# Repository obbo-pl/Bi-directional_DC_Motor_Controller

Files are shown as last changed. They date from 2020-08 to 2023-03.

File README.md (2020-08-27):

# Bi-directional_DC_Motor_Controller
RC Bi-directional DC Motor Speed Controller

##### Main features:

- supply voltage: 7.0 - 20.0V,
- average current: 10A, maximum instantaneous current: 140A,
- BEC 5V 1,2A,
- protection against reverse battery polarity,
- on/off switch controlled by logic level,
- calibration of the adjustment range with automatic saving of settings,
- protection against engine starting when starting the system,
- Cut-off, engine shutdown or speed reduction,
- choice of: linear and nonlinear RPM control characteristics,
- speed regulation smoothing filter,
- Fail-safe, engine shutdown in the event of signal loss,
- 3 quick configuration jumpers,
- brake,
- parameter configuration via serial port (9600bps).

### Hardware & Firmware.

These sections provide information on building a hardware, including schematics, PCBs, and firmware.

For more information: [www.obbo.pl](http://obbo.pl/dc-controller)

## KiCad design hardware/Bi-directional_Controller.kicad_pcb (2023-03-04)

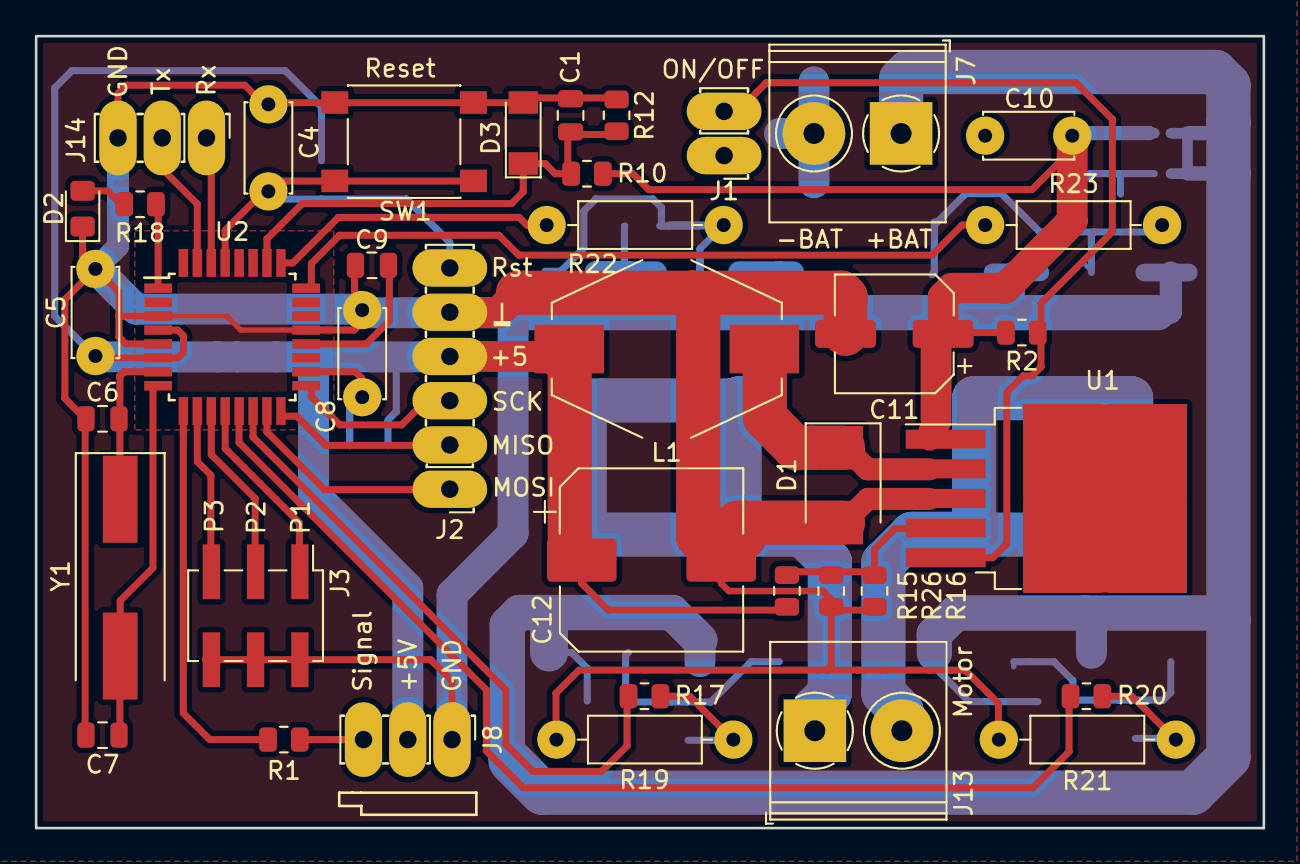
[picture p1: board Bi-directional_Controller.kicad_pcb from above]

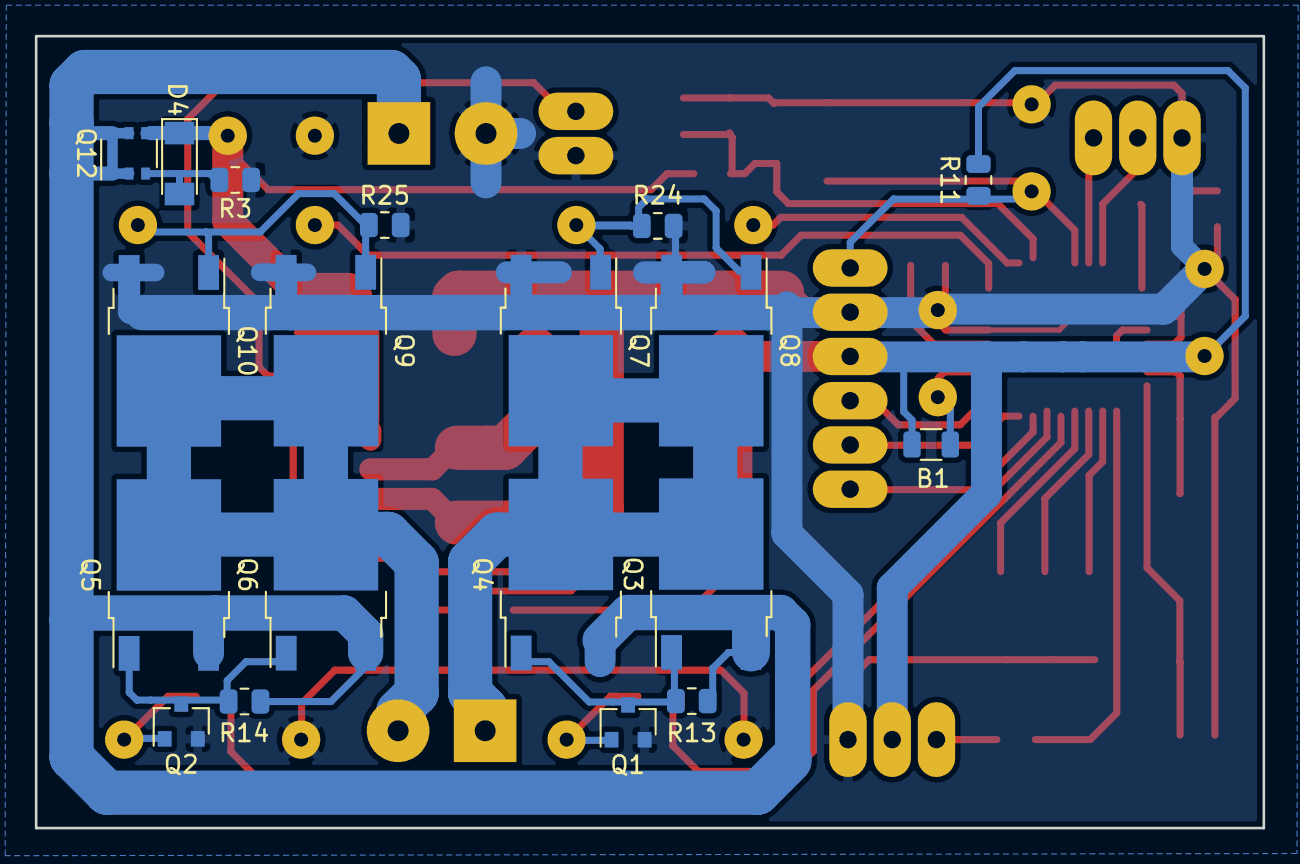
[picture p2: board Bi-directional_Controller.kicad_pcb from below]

Board: 2 copper layers, 70.5 x 45.5 mm, 58 parts (19 on the bottom side), 38 nets.

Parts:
B1: bead; L_0805K
C1, C9: 100n; C_0805_2012Metric
C4, C5, C8, C10: 100n; C_Disc_D5.0mm_W2.5mm_P5.00mm_PAD
C6, C7: 15p; C_0805_2012Metric
C11: 100u/35V; CP_Elec_6.3x5.9
C12: 1000u/10V; CP_Elec_10x10
D1: B340; D_SMB
D2: LED; LED_0805_2012Metric_Pad1.15x1.40mm_HandSolder
D3: 4V7; D_MiniMELF
D4: 8v2; D_MiniMELF
J1: ON/OFF; PinHeader_1x02_P2.54mm_Vertical_PAD
J2: Conn_01x06; PinHeader_1x06_P2.54mm_Vertical_PAD
J3: Conn_02x03_Odd_Even; PinHeader_2x03_P2.54mm_Vertical_SMD
J7: BAT 12V; TerminalBlock_Degson_DG128-5.0-02P
J8: CH1; PinHeader_1x03_P2.54mm_Vertical_PAD
J13: MOTOR; TerminalBlock_Degson_DG128-5.0-02P
J14: Serial; PinHeader_1x03_P2.54mm_Vertical_PAD
L1: 100uH; L_SMD_Ferrite_X13mm_Y10mm_H5mm_HandSoldering
Q1, Q2: BSS138; SOT-23
Q3, Q4, Q5, Q6: AOD403; TO-252-2-DPAK
Q7, Q8, Q9, Q10: AOD240; TO-252-2-DPAK
Q12: AO6401A; TSOP-6_1.65x3.05mm_P0.95mm
R1, R18: 330; R_0805_2012Metric
R2, R3, R11, R15: 10k; R_0805_2012Metric
R10: 22k*; R_0805_2012Metric
R12, R26: 4k7; R_0805_2012Metric
R13, R14, R24, R25: 22k; R_0805_2012Metric
R16: 11k*; R_0805_2012Metric
R17, R20: 220; R_0805_2012Metric
R19, R21: 22k; R_Axial_DIN0207_L6.3mm_D2.5mm_P10.16mm_Horizontal_PAD
R22, R23: 220; R_Axial_DIN0207_L6.3mm_D2.5mm_P10.16mm_Horizontal_PAD
SW1: RESET; SW_SPST_PTS645
U1: LM2576HVS-5; TO-263-5_TabPin6
U2: ATmega8-16AU; TQFP-32_7x7mm_P0.8mm
Y1: 16MHz; Crystal_SMD_HC49-SD_HandSoldering

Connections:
+5V: B1.1, C5.1, C12.1, J2.4, J8.2, L1.2, R11.1, R15.2, U2.4, U2.6
+12V: C10.1, C11.1, D4.1, Q12.4, R2.2, R10.1, U1.1
CH1: R1.1, U2.9
DIR_L: R20.2, U2.13
DIR_R: R17.2, U2.14
GND: C1.2, C4.2, C5.2, C6.2, C7.2, C8.2, C9.2, C10.2, C11.2, C12.2, D1.2, D2.1, D3.2, J1.1, J2.5, J3.2, J3.4, J3.6, J7.2, J8.1, J14.3, Q1.2, Q2.2, Q7.3, Q8.3, Q9.3, Q10.3, R3.1, R12.2, R16.2, R19.1, R21.2, R24.1, R25.1, R26.1, SW1.1, U1.3, U2.3, U2.5, U2.21
unnamed: B1.2, C8.1, U2.18
unnamed: C4.1, J2.6, R11.2, SW1.2, U2.29
unnamed: C6.1, U2.7, Y1.1
unnamed: C7.1, U2.8, Y1.2
unnamed: C9.1, U2.20
unnamed: D1.1, L1.1, U1.2
unnamed: D2.2, R18.2
unnamed: D4.2, Q12.3, R3.2
unnamed: J1.2, R2.1, U1.5
unnamed: J2.1, U2.15
unnamed: J2.2, U2.16
unnamed: J2.3, U2.17
unnamed: J3.1, U2.12
unnamed: J3.3, U2.11
unnamed: J3.5, U2.10
unnamed: J8.3, R1.2
unnamed: J13.1, Q3.2, Q4.2, Q7.2, Q8.2
unnamed: J13.2, Q5.2, Q6.2, Q9.2, Q10.2
unnamed: J14.1, U2.30
unnamed: J14.2, U2.31
unnamed: Q1.1, R17.1, R19.2
unnamed: Q1.3, Q3.1, Q4.1, R13.1
unnamed: Q2.1, R20.1, R21.1
unnamed: Q2.3, Q5.1, Q6.1, R14.1
unnamed: Q7.1, Q8.1, R22.2, R24.2
unnamed: Q9.1, Q10.1, R23.2, R25.2
unnamed: R15.1, R16.1, R26.2, U1.4
unnamed: R18.1, U2.1
PULS_L: R22.1, U2.25
PULS_R: R23.1, U2.24
V_BAT: J7.1, Q3.3, Q4.3, Q5.3, Q6.3, Q12.1, Q12.2, Q12.5, Q12.6, R13.2, R14.2
V_TEST: C1.1, D3.1, R10.2, R12.1, U2.26

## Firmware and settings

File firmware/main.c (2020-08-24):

/*
 * main.c
 *
 * Created: 12.08.2019 13:17:11
 * Atmel Studio 6 (Version: 6.2.1563 - Service Pack 2)
 * AVR/GNU C Compiler : 4.8.1
 *  Author: Krzysztof Markiewicz
 *  www.obbo.pl
 *
 * This program is distributed under the terms of the GNU General Public License
 */ 

#include <avr/io.h>
#include <avr/interrupt.h>
#include <util/delay.h>
#include <avr/eeprom.h>
#include <avr/pgmspace.h>
#include <stdlib.h>
#include <stdbool.h>
#include "main.h"
#include "lowpass_filter.h"
#include "types.h"
#include "delays.h"
#include "cbuffer.h"
#include "usart.h"
#include "terminal.h"
#include "terminal_commands.h"
#include "adconversion.h"
#include "bridge.h"
#include "led.h"


// resource:
// timer0 - common timers
// timer1 - checks the signal from the receiver
// timer2 - motor PWM
// ADC - checks battery voltage
// UART - serial communication (9600) for advanced configuration



#define VERSION_MAJOR				"1"
#define VERSION_MINOR				"0"
#define DEVICE_INFO_SIZE			40
const char DEVICE_INFO[DEVICE_INFO_SIZE]	PROGMEM = "DC " VERSION_MAJOR "." VERSION_MINOR " (build: " __DATE__ " " __TIME__ ")\n\r";

uint8_t EEMEM EEMEM_curve[256] = {0x00, 0x06, 0x0c, 0x12, 0x12, 0x12, 0x12, 0x12, 0x12, 0x12, 0x12, 0x12, 0x12, 0x12, 0x12, 0x13,
				  0x13, 0x13, 0x13, 0x13, 0x13, 0x13, 0x14, 0x14, 0x14, 0x14, 0x15, 0x15, 0x15, 0x15, 0x16, 0x16,
				  0x16, 0x16, 0x17, 0x17, 0x17, 0x18, 0x18, 0x18, 0x19, 0x19, 0x19, 0x1a, 0x1a, 0x1b, 0x1b, 0x1b,
				  0x1c, 0x1c, 0x1d, 0x1d, 0x1e, 0x1e, 0x1e, 0x1f, 0x1f, 0x20, 0x20, 0x21, 0x21, 0x22, 0x23, 0x23,
				  0x24, 0x24, 0x25, 0x25, 0x26, 0x27, 0x27, 0x28, 0x28, 0x29, 0x2a, 0x2a, 0x2b, 0x2c, 0x2c, 0x2d,
				  0x2e, 0x2e, 0x2f, 0x30, 0x30, 0x31, 0x32, 0x33, 0x33, 0x34, 0x35, 0x36, 0x37, 0x37, 0x38, 0x39,
				  0x3a, 0x3b, 0x3b, 0x3c, 0x3d, 0x3e, 0x3f, 0x40, 0x40, 0x41, 0x42, 0x43, 0x44, 0x45, 0x46, 0x47,
				  0x48, 0x49, 0x4a, 0x4a, 0x4b, 0x4c, 0x4d, 0x4e, 0x4f, 0x50, 0x51, 0x52, 0x53, 0x54, 0x55, 0x56,
				  0x57, 0x58, 0x59, 0x5a, 0x5c, 0x5d, 0x5e, 0x5f, 0x60, 0x61, 0x62, 0x63, 0x64, 0x65, 0x66, 0x68,
				  0x69, 0x6a, 0x6b, 0x6c, 0x6d, 0x6e, 0x70, 0x71, 0x72, 0x73, 0x74, 0x75, 0x77, 0x78, 0x79, 0x7a,
				  0x7b, 0x7d, 0x7e, 0x7f, 0x80, 0x82, 0x83, 0x84, 0x85, 0x87, 0x88, 0x89, 0x8a, 0x8c, 0x8d, 0x8e,
				  0x90, 0x91, 0x92, 0x93, 0x95, 0x96, 0x97, 0x99, 0x9a, 0x9b, 0x9d, 0x9e, 0x9f, 0xa1, 0xa2, 0xa3,
				  0xa5, 0xa6, 0xa7, 0xa9, 0xaa, 0xac, 0xad, 0xae, 0xb0, 0xb1, 0xb2, 0xb4, 0xb5, 0xb7, 0xb8, 0xb9,
				  0xbb, 0xbc, 0xbe, 0xbf, 0xc0, 0xc2, 0xc3, 0xc5, 0xc6, 0xc7, 0xc9, 0xca, 0xcc, 0xcd, 0xcf, 0xd0,
				  0xd1, 0xd3, 0xd4, 0xd6, 0xd7, 0xd9, 0xda, 0xdc, 0xdd, 0xde, 0xe0, 0xe1, 0xe3, 0xe4, 0xe6, 0xe7,
				  0xe9, 0xea, 0xec, 0xed, 0xee, 0xf0, 0xf1, 0xf3, 0xf4, 0xf6, 0xf7, 0xf9, 0xfa, 0xfc, 0xfd, 0xff
};
								
uint8_t curve[256];
#ifdef ADCONVERSION_8_BIT_PRECISION
uint8_t EEMEM EEMEM_battery_cut = 0xaa;
#else
uint16_t EEMEM EEMEM_battery_cut = 0x01aa;
#endif
uint8_t EEMEM EEMEM_battery_divider = 0x12; 
uint8_t EEMEM EEMEM_custom_filter_length = SPEED_FILTER_DEFAULT;
uint8_t EEMEM EEMEM_speed_limit = 0x80;

uint16_t EEMEM EEMEM_channel_maximum = CHANNEL_PULSE_MAXIMUM;
uint16_t EEMEM EEMEM_channel_neutral = CHANNEL_PULSE_NEUTRAL;
uint16_t EEMEM EEMEM_channel_minimum = CHANNEL_PULSE_MINIMUM;
uint8_t EEMEM EEMEM_channel_saved = 0x00;

uint8_t EEMEM EEMEM_brake_enabled = 0x00;

uint8_t error_recovery = 0b00010000;

uint8_t configuration_jumpers = 0x00;
LPFu16_t filter_speed;
LPFu16_t filter_adc;

uint8_t calibration_progres = 0;

DCCON_t state = {.errors = 0,
		 .errors_prev = 0,
		 .channel_neutral = 0x0000,
		 .channel_maximum = 0x0000,
		 .channel_minimum = 0xffff,
		 .channel_move_maximum = 0,
		 .channel_move_minimum = 0,
		 .speed_max = SPEED_MAX,
		 .device_info = DEVICE_INFO,
};

DELAY_t timer_adc;
DELAY_t timer_signal_ms;
#if (defined(__AVR_ATmega328__) || defined(__AVR_ATmega328P__))
DELAY_t timer_led_status_ms;
#endif

LED_t led_status;

CircularBuffer_t cbuffer;
DCTERMINAL_t terminal;


void main_InitTimers(void);
void main_InitPulseTimer(void);
void main_StartPulseTimer(void);
void main_StopPulseTimer(void);
uint16_t main_ReadPulseTimer(void);
bool main_IsPulseTimerOverload(void);
void main_InitMotorTimer(void);
void main_StartMotorTimer(uint8_t length);
uint8_t main_ReadMotorTimer(void);
void main_InitCommonTimer(void);
void main_InitExpCurve(void);
bool main_CheckChannelInput(uint16_t *val, bool verify);
bool main_VerifyChannelValue(uint16_t *val);
void main_UpdateRecovery(int recovery_delay);
void main_CheckBattery(void);
void main_InitIO(void);
void main_FlashLedShort(void);
void main_FlashLedLong(void);
void main_SetLedOff(void);
void main_SetLedOn(void);
void main_ShowStatus(uint8_t status, uint8_t count);
void main_ReadSetup(void);
void main_CalculateChannelConstants(void);
void main_ApplyReduceSpeed(uint8_t *speed);
uint32_t main_ApplyZoneNeutral(uint32_t pulse);
void main_ApplySpeedFilter(uint32_t *speed, uint16_t new_speed);
void main_ApplySpeedCurve(uint8_t *speed);
void main_RecalculateSpeed(BRIDGE_t *rotation, uint16_t pulse_length);
void main_SetBrake(uint32_t pulse, BRIDGE_t *rotation);
void main_ReadConfigurationJumper(void);
void main_SaveSetup(void);
void main_SaveCalibration(void);
void main_ReadCalibration(void);
bool main_IsCalibrationSaved(void);
void main_ClearCalibration(void);


int main(void) 
{
	main_InitIO();
	bridge_Init(&state.rotation);
	main_InitExpCurve();
	main_ReadConfigurationJumper();
	adc_Init(glue2(ADCONVERSION_MUX_ADC,CONFIG_BAT_PORTC_PIN));
	main_ReadSetup();

	usart_Init();
	cbuffer_Init(&cbuffer);
	terminal_Init(&terminal, &cbuffer);
	terminal_commands_Init(&state);
	
 	terminal_SendNL(&cbuffer, true);
 	terminal_PrintPM(&cbuffer, state.device_info, true);
	terminal_FlushOutBuffer(&cbuffer);

	delays_Init(&timer_signal_ms, SIGNAL_LOST_TIMEOUT_MS);
	delays_Pause(&timer_signal_ms);
	delays_Init(&timer_adc, ADC_CONVERSION_TIMEOUT_MS);
#if (defined(__AVR_ATmega328__) || defined(__AVR_ATmega328P__))
	delays_Init(&timer_led_status_ms, LED_UPDATE_INTERVAL_MS);
	delays_Pause(&timer_led_status_ms);
#endif	
	lpfilter_Set(&filter_adc, ADC_FILTER);
#ifdef ADCONVERSION_8_BIT_PRECISION	
	lpfilter_Fill(&filter_adc, 0x00ff);
#else
	lpfilter_Fill(&filter_adc, 0x03ff);
#endif
	main_InitTimers();
	main_FlashLedShort();
	_delay_ms(400);
	if (testbit(configuration_jumpers, JUMPER_P3_SERVICE_MODE_bp)) {
		state.channel_neutral = CHANNEL_PULSE_NEUTRAL;
		state.channel_maximum = CHANNEL_PULSE_MAXIMUM + CHANNEL_PULSE_ZONE_NEUTRAL + CHANNEL_PULSE_ERROR;
		state.channel_minimum = CHANNEL_PULSE_MINIMUM - CHANNEL_PULSE_ZONE_NEUTRAL - CHANNEL_PULSE_ERROR;
		main_ClearCalibration();
		delays_Pause(&timer_adc);
		goto READY_TO_RUN;
	}
	main_CheckBattery();
	if (state.errors) {
		while (1) {
			main_ShowStatus(state.errors, 8);
			_delay_ms(3000);
		}
	}
	delays_Pause(&timer_adc);
	// wait for pulse from receiver
	uint8_t pulses = 0;
	while (pulses < (25)) {
		if (main_CheckChannelInput(&state.channel_value, false)) pulses += 1;
	}
	setbit(calibration_progres, CALIBRATION_SIGNAL_bp);
	main_ShowStatus(calibration_progres, 1);
	_delay_ms(1000);
	// skip calibration
	if (main_IsCalibrationSaved()) {
		main_ReadCalibration();
		goto SKIP_CALIBRATION;
	}
	// wait for stable pulse in zone "neutral"
	pulses = 0;
	while (pulses < (25)) {
		if (main_CheckChannelInput(&state.channel_value, false)) {
			if ((state.channel_value > (CHANNEL_PULSE_NEUTRAL - CHANNEL_PULSE_ERROR)) 
				&& (state.channel_value < (CHANNEL_PULSE_NEUTRAL + CHANNEL_PULSE_ERROR))) {
				pulses += 1;
			} else {
				pulses = 0;
			}
		}
	}
	// measure length of "neutral" position
	pulses = 0;
	while (pulses < (16)) {
		if (main_CheckChannelInput(&state.channel_value, false)) {
			if ((state.channel_value > (CHANNEL_PULSE_NEUTRAL - CHANNEL_PULSE_ERROR)) 
				&& (state.channel_value < (CHANNEL_PULSE_NEUTRAL + CHANNEL_PULSE_ERROR))) {
				pulses += 1;
				state.channel_neutral += state.channel_value;
			} else {
				pulses = 0;
				state.channel_neutral = 0;
			}
		}
	}
	state.channel_neutral = state.channel_neutral >> 4;
	setbit(calibration_progres, CALIBRATION_NEUTRAL_bp);
	main_ShowStatus(calibration_progres, 2);
	// wait for stable pulse in zone "maximum" and measure maximum pulse length 
	pulses = 0;
	while (pulses < (25)) {
		if (main_CheckChannelInput(&state.channel_value, false)) {
			if (state.channel_value > CHANNEL_PULSE_MAXIMUM) {
				pulses += 1;
				if (state.channel_value > state.channel_maximum) state.channel_maximum = state.channel_value;
			} else {
				pulses = 0;
				state.channel_maximum = 0x0000;
			}
		}
	}
	setbit(calibration_progres, CALIBRATION_MAXIMUM_bp);
	main_ShowStatus(calibration_progres, 3);
	// wait for stable pulse in zone "minimum" and measure minimum pulse length
	pulses = 0;
	while (pulses < (25)) { 
		if (main_CheckChannelInput(&state.channel_value, false)) {
			if (state.channel_value < CHANNEL_PULSE_MINIMUM) {
				pulses += 1;
				if (state.channel_value < state.channel_minimum) state.channel_minimum = state.channel_value;
			} else {
				pulses = 0;
				state.channel_minimum = 0xffff;
			}
		}
	}
	setbit(calibration_progres, CALIBRATION_MINIMUM_bp);
	main_ShowStatus(calibration_progres, 4);
	main_SaveCalibration();
SKIP_CALIBRATION:
	// wait for return to zone "neutral"
	pulses = 0;
	while (pulses < (25)) {
		if (main_CheckChannelInput(&state.channel_value, false)) {
			if ((state.channel_value > (state.channel_neutral - CHANNEL_PULSE_ZONE_NEUTRAL)) 
				&& (state.channel_value < (state.channel_neutral + CHANNEL_PULSE_ZONE_NEUTRAL))) {
				pulses += 1;
			} else {
				pulses = 0;
			}
		}
	}
	setbit(calibration_progres, CALIBRATION_READY_bp);
READY_TO_RUN:
	if (testbit(configuration_jumpers, JUMPER_P1_SPEED_FILTER_bp)) {
		lpfilter_Set(&filter_speed, state.custom_filter_length);
	} else {
		lpfilter_Set(&filter_speed, SPEED_FILTER_DEFAULT); 
	}
	// start rotation
	state.rotation.speed = 0;
	if (!testbit(configuration_jumpers, JUMPER_P3_SERVICE_MODE_bp)) main_StartMotorTimer(100);
	
	main_CalculateChannelConstants();	
	lpfilter_Fill(&filter_speed, state.channel_neutral_x2);
	delays_Reset(&timer_signal_ms);
	
#if (defined(__AVR_ATmega328__) || defined(__AVR_ATmega328P__))
	delays_Reset(&timer_led_status_ms);
	led_Init(&led_status, PORT_REG_O(CONFIG_LED));
	led_SetLed(&led_status, true, false);
#else
	main_SetLedOn();
#endif
	sei();
	uint8_t command_length;
	bool new_channel_value = false;
	while (1) {
		// error recovery 
		state.errors &= ~(error_recovery);
		// check signal
		new_channel_value = main_CheckChannelInput(&(state.channel_value), true);
		// fail-safe
		if (delays_Check(&timer_signal_ms) || (state.recovery > 0)) {
 			setbit(state.errors, ERROR_CHANNEL_LOST_bp);
			state.channel_value = state.channel_neutral;
			new_channel_value = true;
		} 
		// closer loop when seeking a signal
		if ((timer_signal_ms.counter < (SIGNAL_LOST_TIMEOUT_MS - SIGNAL_PULSE_DISTANCE_MIN_MS)) 
		     && (timer_signal_ms.counter > (SIGNAL_LOST_TIMEOUT_MS - SIGNAL_PULSE_DISTANCE_MAX_MS))) continue;
		// convert pulse length to rotation
		if (new_channel_value) {  
			main_RecalculateSpeed(&state.rotation, state.channel_value);
			main_ApplyReduceSpeed(&state.rotation.speed);
			new_channel_value = false;
		}
		// check terminal buffer
		terminal_SendOutBuffer(&cbuffer);
		if (terminal.change_to_write) main_SaveSetup();
		if (terminal.input_is_full) terminal_DropInputBuffer(&terminal);
		if (terminal_FindNewLine(&terminal, &command_length)) terminal_ParseCommand(&terminal, command_length);
		// check state
		if (delays_Check(&timer_adc)) setbit(state.errors, ERROR_ADC_TIMEOUT_bp);
		main_CheckBattery();
#if (defined(__AVR_ATmega328__) || defined(__AVR_ATmega328P__))
		// error state signaling
		if (delays_Check(&timer_led_status_ms)) {
			led_Update(&led_status);
			delays_Reset(&timer_led_status_ms);
		}
		if (state.errors != state.errors_prev) {
			if (state.errors) {
				led_SetLed(&led_status, true, true);
				if (testbit(state.errors, ERROR_BATTERY_LOW_bp)) {
					led_SetTimers(&led_status, 50, 45);
				} else if (testbit(state.errors, ERROR_CHANNEL_LOST_bp)) {
					led_SetTimers(&led_status, 10, 5);
				} else {
					led_SetTimers(&led_status, 50, 5);
				}
			} else {
				led_SetLed(&led_status, true, false);
			}
			state.errors_prev = state.errors;
		}
#endif
	}
}

#if (defined(__AVR_ATmega8__))
ISR(USART_RXC_vect)
#elif (defined(__AVR_ATmega88A__) || defined(__AVR_ATmega88PA__) || defined(__AVR_ATmega328__) || defined(__AVR_ATmega328P__))
ISR(USART_RX_vect)
#endif
{
	terminal_InterruptHandler(&terminal);
}

ISR(TIMER0_OVF_vect)
{
	delays_Update(&timer_signal_ms, TIMER_COMMON_OVF_MS);
	delays_Update(&timer_adc, TIMER_COMMON_OVF_MS);
#if (defined(__AVR_ATmega328__) || defined(__AVR_ATmega328P__))
	delays_Update(&timer_led_status_ms, TIMER_COMMON_OVF_MS);
#endif
}

#if (defined(__AVR_ATmega8__))
ISR(TIMER2_COMP_vect)
{
	// stop timer
	TCCR2 &= ~((1 << CS22) | (1 << CS21) | (1 << CS20));
	bridge_InterruptHandler(state.rotation, main_StartMotorTimer);
}
#elif (defined(__AVR_ATmega88A__) || defined(__AVR_ATmega88PA__) || defined(__AVR_ATmega328__) || defined(__AVR_ATmega328P__))
ISR(TIMER2_COMPA_vect)
{
	// stop timer
	TCCR2B &= ~((1 << CS22) | (1 << CS21) | (1 << CS20));
	bridge_InterruptHandler(state.rotation, main_StartMotorTimer);
}
#endif

void main_InitIO(void)
{
	SET_PIN_LEVEL_LOW(CONFIG_LED);
	SET_PIN_AS_OUT(CONFIG_LED);

	SET_PIN_PULLUP(CONFIG_P1);
	SET_PIN_PULLUP(CONFIG_P2);
	SET_PIN_PULLUP(CONFIG_P3);
	
	SET_PIN_PULLUP(CONFIG_CH1);
}

void main_InitTimers(void)
{
	main_InitPulseTimer();
	main_InitMotorTimer();
	main_InitCommonTimer();
}

void main_InitPulseTimer(void)
{
	// Timer1 (16-bit)
	TCCR1B &= ~((1 << CS12) | (1 << CS11) | (1 << CS10));
#if (defined(__AVR_ATmega8__))
	TIFR |= (1 << TOV1);
#elif (defined(__AVR_ATmega88A__) || defined(__AVR_ATmega88PA__) || defined(__AVR_ATmega328__) || defined(__AVR_ATmega328P__))
	TIFR1 |= (1 << TOV1);
#endif
}

void main_StartPulseTimer(void)
{
	TCNT1H = 0;
	TCNT1L = 0;
#if (defined(__AVR_ATmega8__))
	TIFR |= (1 << TOV1);
#elif (defined(__AVR_ATmega88A__) || defined(__AVR_ATmega88PA__) || defined(__AVR_ATmega328__) || defined(__AVR_ATmega328P__))
	TIFR1 |= (1 << TOV1);
#endif
	TCCR1B |= (1 << CS11) | (1 << CS10);
}

void main_StopPulseTimer(void)
{
	TCCR1B &= ~((1 << CS12) | (1 << CS11) | (1 << CS10));
}

uint16_t main_ReadPulseTimer(void)
{
	uint16_t result;
	unsigned char sreg;
	sreg = SREG;
	cli();
	result = TCNT1;
	SREG = sreg;
	sei();
	return result;
}

bool main_IsPulseTimerOverload(void)
{
#if (defined(__AVR_ATmega8__))
	return (TIFR >> TOV1) & 0x01;
#elif (defined(__AVR_ATmega88A__) || defined(__AVR_ATmega88PA__) || defined(__AVR_ATmega328__) || defined(__AVR_ATmega328P__))
	return (TIFR1 >> TOV1) & 0x01;
#endif
}

void main_InitMotorTimer(void)
{
#if (defined(__AVR_ATmega8__))
	TCCR2 = (1 << WGM21);
	TCCR2 = (1 << FOC2);
	TIMSK = (1 << OCIE2);
#elif (defined(__AVR_ATmega88A__) || defined(__AVR_ATmega88PA__) || defined(__AVR_ATmega328__) || defined(__AVR_ATmega328P__))
	TCCR2A = (1 << WGM21);
	TCCR2B = (1 << FOC2A);
	TIMSK2 = (1 << OCIE2A);
#endif
}

void main_StartMotorTimer(uint8_t length)
{
#if (defined(__AVR_ATmega8__))
	OCR2 = length;
	TCCR2 |= (1 << CS22);
#elif (defined(__AVR_ATmega88A__) || defined(__AVR_ATmega88PA__) || defined(__AVR_ATmega328__) || defined(__AVR_ATmega328P__))
	OCR2A = length;
	TCCR2B |= (1 << CS22);
#endif
}

uint8_t main_ReadMotorTimer(void)
{
	return TCNT2;
}

void main_InitCommonTimer(void)
{
#if (defined(__AVR_ATmega8__))
	TIMSK |= (1 << TOIE0);
	TCCR0 = (1 << CS02);
#elif (defined(__AVR_ATmega88A__) || defined(__AVR_ATmega88PA__) || defined(__AVR_ATmega328__) || defined(__AVR_ATmega328P__))
	TIMSK0 |= (1 << TOIE0);
	TCCR0B = (1 << CS02);
#endif
}

bool main_CheckChannelInput(uint16_t *val, bool verify)
{
	// check the channel pulse length, it should be between 1ms and 2ms 
	// timer prescaler is set to 4us per tick
	// then should count from 250 to 500 tick per pulse
	// the result (val) is converted into microseconds
	// returns "true" and updates "val" when a new pulse occurs
	bool changed = false;
	uint8_t signal_level = READ_PIN(CONFIG_CH1);
	if (state.signal_level_prev != signal_level) {
		if (signal_level == CHANNEL_LEVEL_ACTIVE) {
			main_StartPulseTimer();
		} else {
			main_StopPulseTimer();
			if (main_IsPulseTimerOverload()) {
				setbit(state.errors, ERROR_TIMER_OVERLOAD_bp);
				state.channel_last = 0xffff;
				main_UpdateRecovery(RECOVERY_DELAY_PL);
   			} else {
				state.channel_last = main_ReadPulseTimer() << 2;
				if (main_VerifyChannelValue(&(state.channel_last)) || !verify) {
					*val = state.channel_last;
					main_UpdateRecovery(-1);
					delays_Reset(&timer_signal_ms);
					changed = true;
				} else {
					setbit(state.errors, ERROR_CHANNEL_OVERRANGE_bp);
					main_UpdateRecovery(RECOVERY_DELAY_PL);
				}
			}
		}
		state.signal_level_prev = signal_level;
	}
	return changed;
}

bool main_VerifyChannelValue(uint16_t *val)
{
	if ((*val < (state.channel_maximum + CHANNEL_PULSE_ERROR)) && (*val > (state.channel_minimum - CHANNEL_PULSE_ERROR))) return true;
	else return false;
}

void main_UpdateRecovery(int recovery)
{
	if (recovery < 0) {
		if (state.recovery > -(ACCEPTED_ERRORS * RECOVERY_DELAY_PL)) state.recovery += recovery;
	} else {
		if (state.recovery < RECOVERY_DELAY_PL) state.recovery += recovery;
	}
}

void main_CheckBattery(void)
{
#ifdef ADCONVERSION_8_BIT_PRECISION
	uint8_t bat;
#else
	uint16_t bat;
#endif
	if (adc_Read(&bat)) {
		delays_Reset(&timer_adc);
		state.battery_voltage = lpfilter_Filter(&filter_adc, bat);
		if (state.battery_voltage < state.battery_cut) {
			state.speed_max = state.speed_limit;
			setbit(state.errors, ERROR_BATTERY_LOW_bp);
		}
	}
}

void main_SetLedOff(void)
{
	SET_PIN_LEVEL_LOW(CONFIG_LED);
}

void main_SetLedOn(void)
{
	SET_PIN_LEVEL_HIGH(CONFIG_LED);
};
	
void main_FlashLedShort(void)
{
	main_SetLedOn();
	_delay_ms(60);
	main_SetLedOff();
	_delay_ms(500);
}

void main_FlashLedLong(void)
{
	main_SetLedOn();
	_delay_ms(500);
	main_SetLedOff();
	_delay_ms(500);
}

void main_ShowStatus(uint8_t status, uint8_t count)
{
	if ((count == 0) || (count > 8)) count = 8;
	for (int i = 0; i < count; i++) {
		if ((status >> i) & 0x01) {
			main_FlashLedLong();
		} else {
			main_FlashLedShort();
		}
	}
}

void main_ApplyReduceSpeed(uint8_t *speed)
{
	if (*speed >= state.speed_max) *speed = state.speed_max;
}

void main_CalculateChannelConstants(void)
{
	state.channel_move_maximum = state.channel_maximum - state.channel_neutral - CHANNEL_PULSE_ZONE_NEUTRAL - CHANNEL_PULSE_ZONE_EXTREMUM;
	state.channel_move_minimum = state.channel_neutral - state.channel_minimum - CHANNEL_PULSE_ZONE_NEUTRAL - CHANNEL_PULSE_ZONE_EXTREMUM;
	state.channel_neutral_x2 = state.channel_neutral << 1;
	state.zone_neutral = CHANNEL_PULSE_ZONE_NEUTRAL;
	state.zone_brake = CHANNEL_PULSE_ZONE_BRAKE; 
	if (state.zone_brake > state.zone_neutral) state.zone_brake = state.zone_neutral;
}

void main_RecalculateSpeed(BRIDGE_t *rotation, uint16_t pulse_length)
{
	uint32_t pulse_filtered;
	// apply filter, 
	// for greater accuracy, filter works on double value of pulse length
	main_ApplySpeedFilter(&pulse_filtered, (pulse_length << 1));
	// convert pulse length to motor direction and speed
	rotation->brake = false;
	if (pulse_filtered > state.channel_neutral_x2) {
		rotation->dir = BRIDGE_DIRECTION_RIGHT;
		pulse_filtered = pulse_filtered - state.channel_neutral_x2;
		main_SetBrake(pulse_filtered, rotation);
		pulse_filtered = main_ApplyZoneNeutral(pulse_filtered);
		pulse_filtered = (pulse_filtered << 8) / state.channel_move_maximum;
	} else {
		rotation->dir = BRIDGE_DIRECTION_LEFT;
		pulse_filtered = state.channel_neutral_x2 - pulse_filtered;
		main_SetBrake(pulse_filtered, rotation);
		pulse_filtered = main_ApplyZoneNeutral(pulse_filtered);
		pulse_filtered = (pulse_filtered << 8) / state.channel_move_minimum;
	}
	pulse_filtered = pulse_filtered >> 1;
	if (pulse_filtered > SPEED_MAX) pulse_filtered = SPEED_MAX;
	uint8_t result = (uint8_t)pulse_filtered;
	// apply curve
	if (testbit(configuration_jumpers, JUMPER_P2_SPEED_CURVE_bp)) {
		main_ApplySpeedCurve(&result);
	}
	rotation->speed = result;
}

void main_SetBrake(uint32_t pulse, BRIDGE_t *rotation) 
{
	if (state.brake_enabled) {
		if (pulse <= state.zone_brake) rotation->brake = true;
	}
}

uint32_t main_ApplyZoneNeutral(uint32_t pulse)
{
	if (pulse > state.zone_neutral) {
		return (pulse - state.zone_neutral);
	} else {
		return 0;
	}
}

void main_ApplySpeedFilter(uint32_t *speed, uint16_t new_speed)
{
	*speed = 0x0000ffff & lpfilter_Filter(&filter_speed, new_speed);
}

void main_ApplySpeedCurve(uint8_t *speed)
{
	*speed = curve[*speed];
}

void main_InitExpCurve(void)
{
	uint8_t i = 0;
	do {
		curve[i] = eeprom_read_byte(&EEMEM_curve[i]);
		i++;
	} while (i);
}

void main_ReadConfigurationJumper(void)
{
	if (!(READ_PIN(CONFIG_P1))) setbit(configuration_jumpers, JUMPER_P1_SPEED_FILTER_bp);
	if (!(READ_PIN(CONFIG_P2))) setbit(configuration_jumpers, JUMPER_P2_SPEED_CURVE_bp);
	if (!(READ_PIN(CONFIG_P3))) setbit(configuration_jumpers, JUMPER_P3_SERVICE_MODE_bp);
}

void main_ReadSetup(void)
{
	#ifdef ADCONVERSION_8_BIT_PRECISION
	state.battery_cut = eeprom_read_byte(&EEMEM_battery_cut);
	#else
	state.battery_cut = eeprom_read_word(&EEMEM_battery_cut);
	#endif
	state.battery_divider = eeprom_read_byte(&EEMEM_battery_divider);
	state.custom_filter_length = eeprom_read_byte(&EEMEM_custom_filter_length);
	state.speed_limit = eeprom_read_byte(&EEMEM_speed_limit);
	state.brake_enabled = eeprom_read_byte(&EEMEM_brake_enabled);
}
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

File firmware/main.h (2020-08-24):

/*
 * main.h
 *
 * Created: 12.08.2019 13:27:43
 * Atmel Studio 6 (Version: 6.2.1563 - Service Pack 2)
 * AVR/GNU C Compiler : 4.8.1
 *  Author: Krzysztof Markiewicz
 *  www.obbo.pl
 *
 * This program is distributed under the terms of the GNU General Public License
 */ 


#ifndef MAIN_H_
#define MAIN_H_


#include <avr/io.h>
#include <avr/eeprom.h>
#include <avr/pgmspace.h>
#include "config.h"
#include "macro.h"



#define TIMER_COMMON_OVF_MS			(4)
#define LED_UPDATE_INTERVAL_MS			(20)
#define SIGNAL_LOST_TIMEOUT_MS			(500)
#define SIGNAL_PULSE_DISTANCE_MIN_MS		(10)
#define SIGNAL_PULSE_DISTANCE_MAX_MS		(30)
#define ADC_CONVERSION_TIMEOUT_MS		(1000)
#define ADC_FILTER				(3)

#define RECOVERY_DELAY_PL			(50)
#define ACCEPTED_ERRORS				(2)
#if (RECOVERY_DELAY_PL * ACCEPTED_ERRORS) >= 32767
#error "Decrease RECOVERY_DELAY_PL or ACCEPTED_ERRORS" 
#endif

#define SPEED_MAX				(0xff)
#define SPEED_FILTER_DEFAULT			(3)

// Sanwa VG6DR
#define CHANNEL_PULSE_MAXIMUM			(1800)
#define CHANNEL_PULSE_MINIMUM			(1200)
#define CHANNEL_PULSE_NEUTRAL			((CHANNEL_PULSE_MAXIMUM + CHANNEL_PULSE_MINIMUM) / 2 )
#define CHANNEL_PULSE_ZONE_NEUTRAL		(80)
#define CHANNEL_PULSE_ZONE_EXTREMUM		(40)
#define CHANNEL_PULSE_ZONE_BRAKE		(50)
#if CHANNEL_PULSE_ZONE_BRAKE >= CHANNEL_PULSE_ZONE_NEUTRAL
#error "CHANNEL_PULSE_ZONE_BRAKE should be lower than CHANNEL_PULSE_ZONE_NEUTRAL"
#endif
#define CHANNEL_PULSE_ERROR			(100)
#define CHANNEL_PULSE_POSITIVE

#ifdef CHANNEL_PULSE_POSITIVE
	#define CHANNEL_LEVEL_ACTIVE		(1)
#else
	#define CHANNEL_LEVEL_ACTIVE		(0)
#endif


enum {
	JUMPER_P1_SPEED_FILTER_bp,
	JUMPER_P2_SPEED_CURVE_bp,
	JUMPER_P3_SERVICE_MODE_bp
};

enum {
	ERROR_BATTERY_LOW_bp,
	ERROR_ADC_TIMEOUT_bp,
	ERROR_TIMER_OVERLOAD_bp,
	ERROR_CHANNEL_OVERRANGE_bp,
	ERROR_CHANNEL_LOST_bp
};

enum {
	CALIBRATION_SIGNAL_bp,
	CALIBRATION_NEUTRAL_bp,
	CALIBRATION_MAXIMUM_bp,
	CALIBRATION_MINIMUM_bp,
	CALIBRATION_READY_bp
};


#endif /* MAIN_H_ */

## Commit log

2019-11-24 symbols update
    [Bi-directional_Controller.kicad_pcb, Bi-directional_Controller.sch]
2019-12-30 added function to store calibration
2020-01-02 disable motor in service mode
2020-07-14 uart_terminal split into separate libraries, support for Atmega328
2020-07-14 support for Atmega328
    [Bi-directional_Controller.sch]
2020-07-15 improved ADC conversion
2020-07-19 motor brake option added
2020-07-30 added error state signaling
    [main.c, main.h]
2020-08-02 calculate PWM only after changing the value
2020-08-24 bridge control based on timer interrupts
2023-03-04 symbol update
    [Bi-directional_Controller.kicad_pcb, Bi-directional_Controller.sch]
